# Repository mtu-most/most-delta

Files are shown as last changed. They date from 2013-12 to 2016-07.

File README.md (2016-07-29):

MOST-delta
==========
Development of the MOST Delta has halted as it has been superceded by <a href="https://github.com/phidiasllc/athena">Athena</a>.

A complete build process is available at http://www.appropedia.org/Delta_Build_Overview:MOST.

<h2>Highlights:</h2>
<ul>
<li>Magnetic tie rod ends</li>
<li>Actively cooled end effector</li>
<li>Attractive</li>
<li>Easy to build</li>
<li>Inexpensive, relatively short BOM</li>
<li>Thorough wiki-based build process with lots of illustrations</li>
<li>A rapidly growing user base</li>
<li>Very robust</li>
</ul>

<h2>Overview</h2>
The MOST delta printer is derived from the original Rostock (http://www.thingiverse.com/thing:17175). The design goal is to stay as true to RepRap ideals as possible, i.e. contain as many printed parts as possible. It's a very robust design and easier to build and calibrate than most delta printers.

<h2>Easter Egg in the SCAD</h2>
Dr. Who fans will want to keep an eye out!

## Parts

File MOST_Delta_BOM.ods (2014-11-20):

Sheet: BOM
Magnetic ball joint version
Part description | Print/Vitamin | Material | UOM | Count | Units | Total units | Functional Unit | Function
608zz bearing | Vitamin | bearing | ea | 6 |  | 6 | Idler end | idler bearing
608zz bearing | Vitamin | bearing | ea | 1 |  | 1 | Extruder drive
LM8UU bearing | Vitamin | bearing | ea | 6 |  | 6 | Apex | carriage linear bearing
MR105zz 5mm x 10mm x 4mm bearing | Vitamin | bearing | ea | 1 |  | 1 | Extruder drive
3/8” od ring magnets | Vitamin | magnet | ea | 12 |  | 12 | Tie rod | tie rod ends
T5 timing belt | Vitamin | belting | mm | 3 | 1350 | 4050 | Apex | timing belt
0.25” OD x 0.222” ID Al tubing | Vitamin | Al tube | mm | 6 | 242 | 1452 | Tie rod | Tie rod
3/8” G25 ball bearings | Vitamin | magnet | mm | 12 | 20 | 240 | Tie rod | tie rod pivot
18-Gauge 2 Conductor | Vitamin | conductor | m | 1 |  | 1 | End effector | hot end power
1m twisted pair | Vitamin | conductor | m | 3 | 1 | 3 | Idler end | limit switch twisted pair
1m twisted pair | Vitamin | conductor | m | 2 |  | 2 | End effector | fan power and hot end thermistor
8mm diameter drill rod | Vitamin | drill rod | mm | 6 | 595 | 3570 | Apex | guide rod
12V 5A power supply | Vitamin | electronics | ea | 1 |  | 1 | Electronics
40mm x 40mm 12v fan | Vitamin | electronics | ea | 1 |  | 1 | End effector | active cooling
Limit switch | Vitamin | electronics | ea | 3 |  | 3 | Electronics | Limit switch
Melzi controller board | Vitamin | electronics | ea | 1 |  | 1 | Electronics
#6 x 3/4” sheet metal screw | Vitamin | fastener | ea | 12 |  | 12 | Motor end | motor end base plate mount
#6 x 3/4” sheet metal screw | Vitamin | fastener | ea | 18 |  | 18 | Motor end | motor end linking board mount
#6 x 3/4” sheet metal screw | Vitamin | fastener | ea | 12 |  | 12 | Idler end | idler end base plate mount
#6 x 3/4” sheet metal screw | Vitamin | fastener | ea | 18 |  | 18 | Idler end | idler end linking board mount
M2 washer | Vitamin | fastener | ea | 6 |  | 6 | Idler end | limit switch mount
M2 x 12mm socket head cap screw | Vitamin | fastener | ea | 6 |  | 6 | Idler end | limit switch mount
M2 x 12mm socket head cap screw | Vitamin | fastener | ea | 1 |  | 1 | End effector | hot end retainer
M3 nut | Vitamin | fastener | ea | 6 |  | 6 | Motor end | motor end pulley
M3 nut | Vitamin | fastener | ea | 6 |  | 6 | Motor end | motor end vertical board mount
M3 nut | Vitamin | fastener | ea | 3 |  | 3 | Carriage | carriage belt terminator mount
M3 nut | Vitamin | fastener | ea | 12 |  | 12 | Idler end | idler end guide rod clamp
M3 nut | Vitamin | fastener | ea | 6 |  | 6 | Idler end | idler end vertical board mount
M3 nut | Vitamin | fastener | ea | 2 |  | 2 | Extruder drive | Preload
M3 nut | Vitamin | fastener | ea | 12 |  | 12 | Frame | Melzi mount
M3 nut | Vitamin | fastener | ea | 12 |  | 12 | Motor end | motor end guide rod clamp
M3 threaded rod | Vitamin | fastener | mm | 6 | 85 | 510 | Motor end | motor end guide rod clamp
M3 threaded rod | Vitamin | fastener | mm | 6 | 85 | 510 | Idler end | idler end guide rod clamp
M3 washer | Vitamin | fastener | ea | 12 |  | 12 | Motor end | motor end motor mount
M3 washer | Vitamin | fastener | ea | 12 |  | 12 | Motor end | motor end guide rod clamp
M3 washer | Vitamin | fastener | ea | 6 |  | 6 | Motor end | motor end vertical board mount
M3 washer | Vitamin | fastener | ea | 3 |  | 3 | Carriage | carriage belt terminator mount
M3 washer | Vitamin | fastener | ea | 12 |  | 12 | Idler end | idler end guide rod clamp
M3 washer | Vitamin | fastener | ea | 12 |  | 12 | Idler end | idler end vertical board mount
M3 washer | Vitamin | fastener | ea | 2 |  | 2 | Extruder drive | Preload
M3 washer | Vitamin | fastener | ea | 16 |  | 16 | Frame | Melzi mount
M3 x 12mm socket head cap screw | Vitamin | fastener | ea | 2 |  | 2 | End effector | fan mount
M3 x 12mm socket head cap screw | Vitamin | fastener | ea | 3 |  | 3 | Carriage | Carriage limit switch adjustment
M3 x 14mm socket head cap screw | Vitamin | fastener | ea | 12 |  | 12 | Motor end | motor end motor mount
M3 x 16mm socket head cap screw | Vitamin | fastener | ea | 3 |  | 3 | Carriage | carriage belt terminator mount
M3 x 25mm socket head cap screw | Vitamin | fastener | ea | 1 |  | 1 | Extruder drive | Motor mount
M3 x 25mm socket head cap screw | Vitamin | fastener | ea | 4 |  | 4 | Frame | Melzi mount
M3 x 30mm socket head cap screw | Vitamin | fastener | ea | 2 |  | 2 | Extruder drive | motor end
M3 x 45mm socket head cap screw | Vitamin | fastener | ea | 2 |  | 2 | Extruder drive | Preload
M3 x 50mm screw | Vitamin | fastener | ea | 6 |  | 6 | Motor end | motor end vertical board mount
M3 x 50mm screw | Vitamin | fastener | ea | 6 |  | 6 | Idler end | idler end vertical board mount
M3 x 6mm button head cap screw | Vitamin | fastener | ea | 1 |  | 1 | Extruder drive | Motor mount
M3 x 8mm set screw | Vitamin | fastener | ea | 6 |  | 6 | Motor end | motor end pulley
M4 nut | Vitamin | fastener | ea | 1 |  | 1 | End effector | Bowden sheath retainer
M4 nut | Vitamin | fastener | ea | 1 |  | 1 | Extruder drive | Infeed tube sheath retainer
M4 nut | Vitamin | fastener | ea | 1 |  | 1 | Extruder drive | Bowden sheath retainer
#6 x 1/2” sheet metal screw | Vitamin | fastener | ea | 2 |  | 2 | Extruder drive | Mounting screws
M8 nut | Vitamin | fastener | ea | 3 |  | 3 | Idler end | idler shaft retainer
M8 washer | Vitamin | fastener | ea | 9 |  | 9 | Idler end | idler shaft
M8 x 40mm hex head bolt | Vitamin | fastener | ea | 3 |  | 3 | Idler end | idler shaft
J-head hot end, 1.75mm x 0.5mm | Vitamin | hot end | ea | 1 |  | 1 | End effector
NEMA17 stepper motor | Vitamin | motor | ea | 1 |  | 1 | Extruder drive
NEMA17 stepper motor | Vitamin | motor | ea | 3 |  | 3 | Motor end | motor end motor mount
12 tooth T5 pulley w/ D shaft | Print | PLA | ea | 3 |  | 3 | Motor end | pulley
Extruder drive body | Print | PLA | ea | 1 |  | 1 | Extruder drive
Airtripper's idler holder | Print | PLA | ea | 1 |  | 1 | Extruder drive
Airtripper's idler shaft | Print | PLA | ea | 1 |  | 1 | Extruder drive
Airtripper's tie rod | Print | PLA | ea | 1 |  | 1 | Extruder drive
carriage | Print | PLA | ea | 3 |  | 3 | Apex | carriage
End effector | Print | PLA | ea | 1 |  | 1 | End effector
End Idler | Print | PLA | ea | 3 |  | 3 | Idler end | idler end
End Motor | Print | PLA | ea | 3 |  | 3 | Motor end | motor end
Fixed belt terminator | Print | PLA | ea | 3 |  | 3 | Apex | long belt terminator
Free belt terminator | Print | PLA | ea | 3 |  | 3 | Apex | short belt terminator
340mm diameter x 12mm plywood | Vitamin | plywood | ea | 2 |  | 2 | Frame | base plates
42mm x 240mm x 12 mm plywood | Vitamin | plywood | ea | 3 |  | 3 | Motor end | Motor end linking board
42mm x 240mm x 12 mm plywood | Vitamin | plywood | ea | 3 |  | 3 | Idler end | Motor end linking board
60mm x 605mm x 12mm plywood | Vitamin | plywood | ea | 3 |  | 3 | Apex | vertical board
1” x 1/4” rubber fuel line | Vitamin | tubing | inch | 1 | 1 | 1 | Extruder drive
4mm OD x 2mm ID PTFE tubing | Vitamin | tubing | mm | 1 | 700 | 700 | End effector | Bowden sheath
4mm OD x 2mm ID PTFE tubing | Vitamin | tubing | mm | 1 | 50 | 50 | Extruder drive | Infeed tube
Small wire ties | Vitamin | wire tie | ea | 10 |  | 10 | Frame
Mk7 drive gear | Vitamin | drive gear | ea | 1 |  | 1 | Extruder drive
USB A to mini B | Vitamin | electronics | ea | 1 |  | 1 | Electronics
Heat shrink tubing | Vitamin | electronics | ea | 10
10” diameter mirror/glass | Vitamin | glass | ea | 1 |  | 1 | Frame | Build platform

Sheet: Pivot Table_BOM_1
Filter
Print/Vitamin | Vitamin
Part description | Material | Data
#6 x 1/2” sheet metal screw | fastener | Sum - Units
 |  | Sum - Count | 2
#6 x 3/4” sheet metal screw | fastener | Sum - Units
 |  | Sum - Count | 60
0.25” OD x 0.222” ID Al tubing | Al tube | Sum - Units | 242
 |  | Sum - Count | 6
1” x 1/4” rubber fuel line | tubing | Sum - Units | 1
 |  | Sum - Count | 1
10” diameter mirror/glass | glass | Sum - Units
 |  | Sum - Count | 1
12V 5A power supply | electronics | Sum - Units
 |  | Sum - Count | 1
18-Gauge 2 Conductor | conductor | Sum - Units
 |  | Sum - Count | 1
1m twisted pair | conductor | Sum - Units | 1
 |  | Sum - Count | 5
3/8” G25 ball bearings | magnet | Sum - Units | 20
 |  | Sum - Count | 12
3/8” od ring magnets | magnet | Sum - Units
 |  | Sum - Count | 12
340mm diameter x 12mm plywood | plywood | Sum - Units
 |  | Sum - Count | 2
40mm x 40mm 12v fan | electronics | Sum - Units
 |  | Sum - Count | 1
42mm x 240mm x 12 mm plywood | plywood | Sum - Units
 |  | Sum - Count | 6
4mm OD x 2mm ID PTFE tubing | tubing | Sum - Units | 750
 |  | Sum - Count | 2
608zz bearing | bearing | Sum - Units
 |  | Sum - Count | 7
60mm x 605mm x 12mm plywood | plywood | Sum - Units
 |  | Sum - Count | 3
8mm diameter drill rod | drill rod | Sum - Units | 595
 |  | Sum - Count | 6
Heat shrink tubing | electronics | Sum - Units
 |  | Sum - Count | 10
J-head hot end, 1.75mm x 0.5mm | hot end | Sum - Units
 |  | Sum - Count | 1
Limit switch | electronics | Sum - Units
 |  | Sum - Count | 3
LM8UU bearing | bearing | Sum - Units
 |  | Sum - Count | 6
M2 washer | fastener | Sum - Units
 |  | Sum - Count | 6
M2 x 12mm socket head cap screw | fastener | Sum - Units
 |  | Sum - Count | 7
M3 nut | fastener | Sum - Units
 |  | Sum - Count | 59
M3 threaded rod | fastener | Sum - Units | 170
 |  | Sum - Count | 12
M3 washer | fastener | Sum - Units
 |  | Sum - Count | 75
M3 x 12mm socket head cap screw | fastener | Sum - Units
 |  | Sum - Count | 5
M3 x 14mm socket head cap screw | fastener | Sum - Units
 |  | Sum - Count | 12
M3 x 16mm socket head cap screw | fastener | Sum - Units
 |  | Sum - Count | 3
M3 x 25mm socket head cap screw | fastener | Sum - Units
 |  | Sum - Count | 5
M3 x 30mm socket head cap screw | fastener | Sum - Units
 |  | Sum - Count | 2
M3 x 45mm socket head cap screw | fastener | Sum - Units
 |  | Sum - Count | 2
M3 x 50mm screw | fastener | Sum - Units
 |  | Sum - Count | 12
M3 x 6mm button head cap screw | fastener | Sum - Units
 |  | Sum - Count | 1
M3 x 8mm set screw | fastener | Sum - Units
 |  | Sum - Count | 6
M4 nut | fastener | Sum - Units
 |  | Sum - Count | 3
M8 nut | fastener | Sum - Units
 |  | Sum - Count | 3
M8 washer | fastener | Sum - Units
 |  | Sum - Count | 9
M8 x 40mm hex head bolt | fastener | Sum - Units
 |  | Sum - Count | 3
Melzi controller board | electronics | Sum - Units
 |  | Sum - Count | 1
Mk7 drive gear | drive gear | Sum - Units
 |  | Sum - Count | 1
MR105zz 5mm x 10mm x 4mm bearing | bearing | Sum - Units
 |  | Sum - Count | 1
NEMA17 stepper motor | motor | Sum - Units
 |  | Sum - Count | 4
Small wire ties | wire tie | Sum - Units
 |  | Sum - Count | 10
T5 timing belt | belting | Sum - Units | 1350
 |  | Sum - Count | 3
USB A to mini B | electronics | Sum - Units
 |  | Sum - Count | 1
Total Sum - Units |  |  | 3129
Total Sum - Count |  |  | 394

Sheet: Sources
Part description | Part number | Unit description | Sold in units of | URL
M2 washer | 7364 | pack | 100 | http://www.boltdepot.com/Product-Details.aspx?product=7364
M2 x 10mm socket head cap screw | 6366 | pack | 100 | http://www.boltdepot.com/Product-Details.aspx?product=6366
M3 nut | 4773 | pack | 1000 | http://www.boltdepot.com/Product-Details.aspx?product=4773
M3 threaded rod | 90024A040 | mm | 1000 | mcmaster.com
M3 washer | 4513 | pack | 1000 | http://www.boltdepot.com/Product-Details.aspx?product=4513
M3 x 12mm socket head cap screw | 6381 | pack | 100 | http://www.boltdepot.com/Product-Details.aspx?product=6381
M3 x 14mm socket head cap screw | 91292A027 | pack | 100 | mcmaster.com
M3 x 16mm socket head cap screw | 6382 | pack | 100 | http://www.boltdepot.com/Product-Details.aspx?product=6382
M3 x 25mm socket head cap screw | 6384 | pack | 100 | http://www.boltdepot.com/Product-Details.aspx?product=6384
M3 x 30mm socket head cap screw | 6385 | pack | 100 | http://www.boltdepot.com/Product-Details.aspx?product=6385
M3 x 45mm socket head cap screw | 6388 | pack | 100 | http://www.boltdepot.com/Product-Details.aspx?product=6388
M3 x 50mm screw | 6389 | pack | 1000 | http://www.boltdepot.com/Product-Details.aspx?product=6389
M3 x 6mm button head cap screw | 92095A179 | pack | 100 | mcmaster.com
M3 x 8mm set screw | 92015A105 | pack | 50 | mcmaster.com
#6 x 3/4” sheet metal screw | 14712 | pack | 1000 | http://www.boltdepot.com/Product-Details.aspx?product=14712
M4 nut | 4774 | pack | 100 | http://www.boltdepot.com/Product-Details.aspx?product=4774
#6 x 1/2” sheet metal screw | 14710 | pack | 100 | http://www.boltdepot.com/Product-Details.aspx?product=14710
M4 x 12mm socket head cap screw | 91292A117 | pack | 100 | mcmaster.com
M4 x 20mm socket head cap screw | 91292A121 | pack | 100 | mcmaster.com
M8 nut | 91828A410 | pack | 50 | mcmaster.com
M8 washer | 93475A270 | pack | 100 | mcmaster.com
M8 x 40mm hex head bolt | 91287A305 | pack | 100 | http://www.boltdepot.com/Product-Details.aspx?product=5817
8mm diameter drill rod | 8116K37 | mm | 1828.8 | mcmaster.com
4mm OD x 2mm ID PTFE tubing | 2129T24 | mm | 304.8 | mcmaster.com
0.25” OD x 0.222” ID Al tubing |  | mm | 1 | http://www3.towerhobbies.com/cgi-bin/wti0001p?&I=LXDTWL&P=7
3/8” od ring magnets | R622CS-P | ea | 2 | https://www.kjmagnetics.com/proddetail.asp?prod=R622CS-P
3/8” G25 ball bearings |  | pack | 1 | http://www.amazon.com/gp/product/B002BBD4SG/ref=oh_details_o08_s00_i00?ie=UTF8&psc=1
608zz bearing |  | pack | 1 | http://rp3d.com
LM8UU bearing |  | pack | 1 | http://rp3d.com
MR105zz 5mm x 10mm x 4mm bearing |  | pack | 1 | http://rp3d.com
T5 timing belt |  | mm | 304.8 | http://shop.polybelt.com/6T5-Open-End-Belt-Roll-Polyurethane-with-Steel-Cords-B6T5-MPS.htm
16-Gauge 2 Conductor |  | mm | 30480 | http://www.amazon.com/Mediabridge-Gauge-Speaker-Wire-Feet/dp/B0044YPN0A
Limit switch | SW767-ND | ea | 1 | http://www.digikey.com/product-detail/en/SS-3GLPT/SW767-ND/664728
12V 5A power supply |  | ea | 1 | Amazon.com
40mm x 40mm 12v fan |  | ea | 1 | http://www.kysanelectronics.com/Products/Detail.php?recordID=7738
Melzi controller board |  | ea | 1 | http://www.rp3d.com/10pcs-melzi-of-3d-printer-p-20.html
NEMA17 stepper motor |  | ea | 1 | http://www.kysanelectronics.com/Products/Detail.php?recordID=7850
J-head hot end, 1.75mm x 0.5mm |  | ea | 1 | hotends.com
1” x 1/4” rubber fuel line |  | mm | 304.8 | http://www.amazon.com/Dayco-80057-Fuel-Line-Roll/dp/B000CIZV7C
Mk7 drive gear |  | ea | 1 | http://twelvepro.com/index.php?route=product/product&product_id=51
USB A to mini B |  | ea | 1 | http://rp3d.com
10” mirror circle |  | ea | 1 | http://www.consumercrafts.com/store/details/catalog/floral-round-mirrors/1635-70

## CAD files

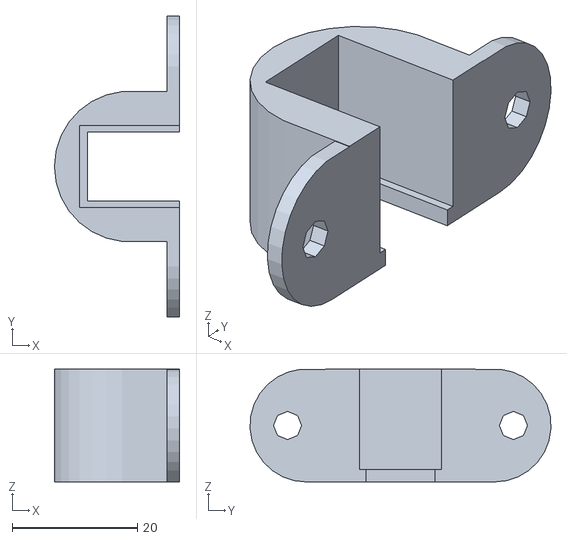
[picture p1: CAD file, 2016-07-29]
STL/barrel_connector.stl
19.9 x 48.0 x 18.0

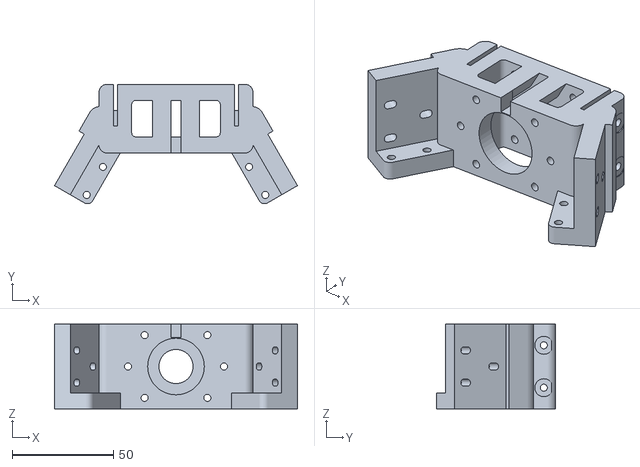
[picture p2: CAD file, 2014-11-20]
STL/end_motor.stl
120.2 x 59.1 x 42.0

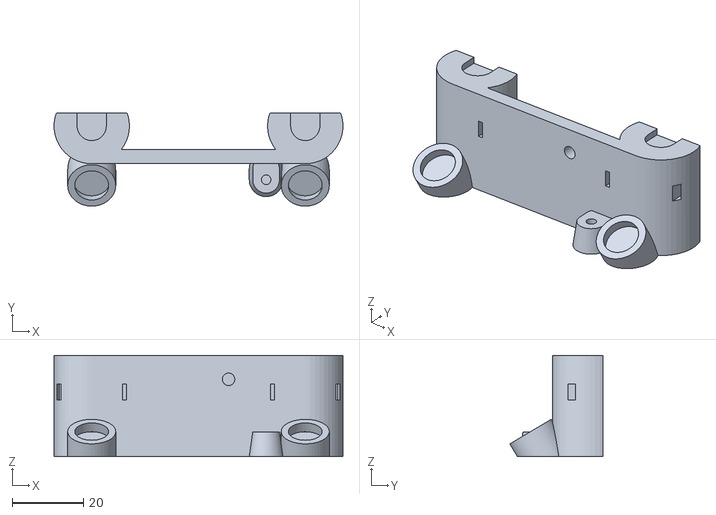
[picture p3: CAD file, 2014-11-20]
STL/carriage.stl
81.2 x 26.2 x 28.5

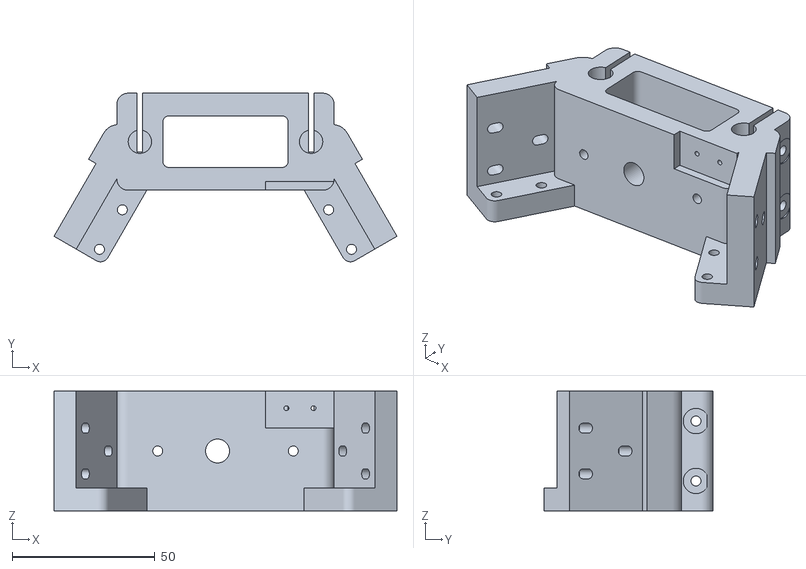
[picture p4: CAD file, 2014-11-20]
STL/end_idler.stl
120.2 x 59.1 x 42.0

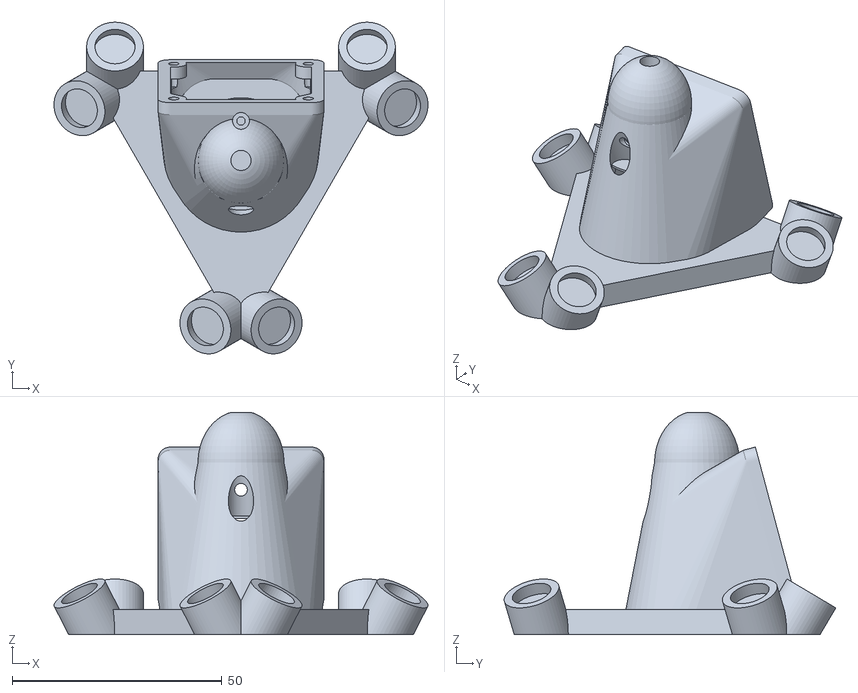
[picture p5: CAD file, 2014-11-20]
STL/effector.stl
89.1 x 79.0 x 52.9

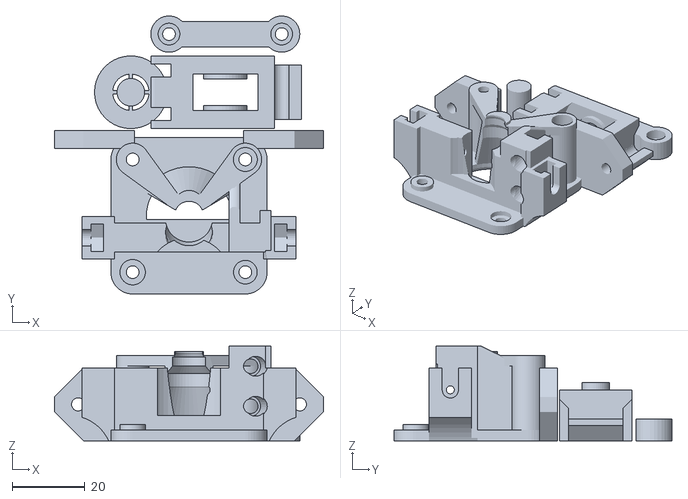
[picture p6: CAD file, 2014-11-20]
STL/extdrive.stl
74.0 x 76.5 x 26.0

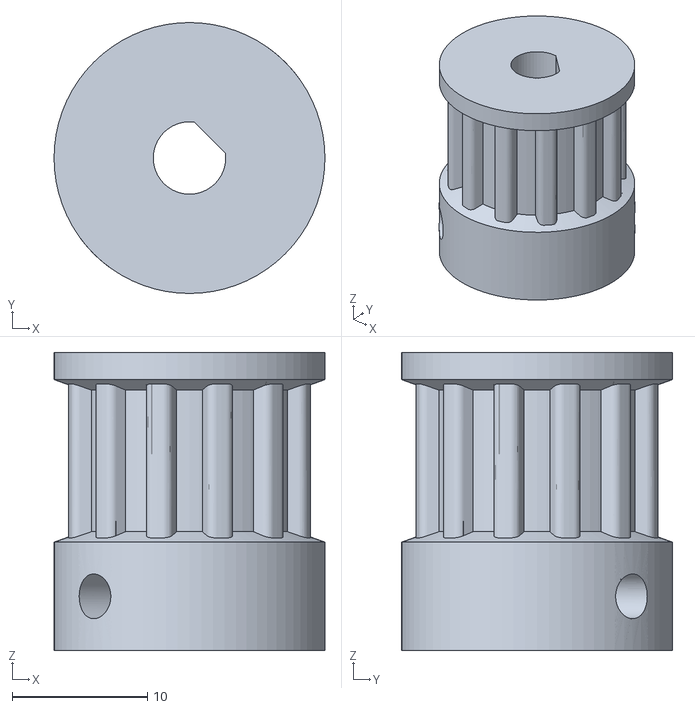
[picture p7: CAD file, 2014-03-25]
STL/12toothT5_Dshaft.stl
20.0 x 20.0 x 22.0

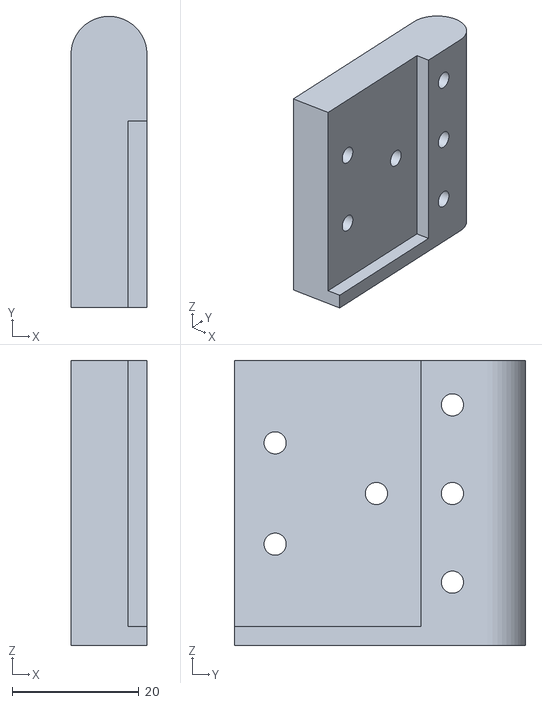
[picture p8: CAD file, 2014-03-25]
STL/linking_brd_template.stl
12.0 x 46.0 x 45.0

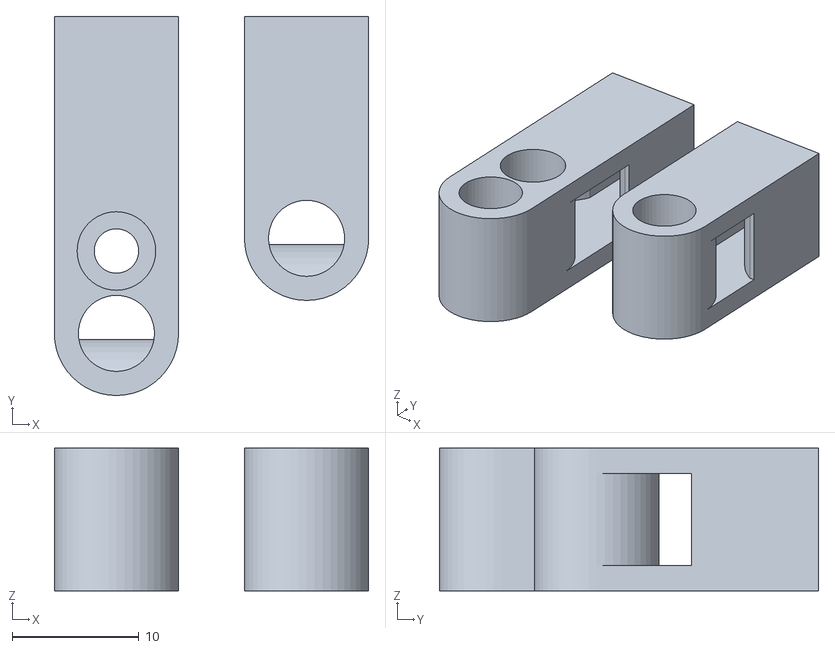
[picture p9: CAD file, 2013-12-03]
STL/belt_terminators.stl
24.8 x 29.9 x 11.2

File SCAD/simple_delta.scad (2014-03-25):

include <fasteners.scad>
include <bearings.scad>
include <NEMA17.scad>
include <cog.scad>
include <Triangles.scad>
include <hotends.scad>
include <belt_terminator.scad>

// [w, l, t] = [y, x, z]
$fn = 48;

//render_part(9);

//plates(3);

magnet_mounts = true;


module plates(plate) {
	if (plate == 1) {
		for (i = [0:2])
			rotate([0, 0, i * 120]) {
				translate([-15, r_effector + 18, t_carriage / 2])
					carriage(dogged = false, magnet_mounts = magnet_mounts, stage_mounts = false);
			
				translate([-20, r_effector + 18, 0])
					rotate([0, 0, 90])
						terminator(l_pass = 10, flag = false, mount = true, magnet = false);
			
				translate([37, r_effector + 10, 0])
					rotate([0, 0, 90])
							terminator(l_pass = 10, flag = 0, mount = 0);
			}

		translate([0, 0, t_effector / 2])
			effector(dalekify = false, magnet_mounts = magnet_mounts);
	}
	
	if (plate == 2) {
		end_motor();
		
		translate([65, 5, 0])
			rotate([0, 0, -60])
				end_motor();
		
		translate([30, -58, 0])
			rotate([0, 0, -60])
				end_motor();
	}

	if (plate == 3) {
		end_idler();
		
		translate([65, 5, 0])
			rotate([0, 0, -60])
				end_idler();
		
		translate([30, -58, 0])
			rotate([0, 0, -60])
				end_idler();
	}
}

module render_part(part_to_render) {
	if (part_to_render == 1) end_motor();

	if (part_to_render == 2) end_idler();

	if (part_to_render == 3) carriage(dogged = false, magnet_mounts = magnet_mounts, stage_mounts = false);

	if (part_to_render == 4) effector(dalekify = false, magnet_mounts = magnet_mounts);

	if (part_to_render == 5) hook();

	if (part_to_render == 6) power_entry();

	if (part_to_render == 7) intermediate();

	if (part_to_render == 8) stage_effector(magnet_mounts = 1);

	if (part_to_render == 9) linking_board_template();

	if (part_to_render == 10) assembly();

	if (part_to_render == 11) camera_carriage();
	
	if (part_to_render == 12) limit_switch_mount();

	if (part_to_render == 13) stage_pcb_dovetail();

	if (part_to_render == 14) stage_pcb_dovetail_clamp();
}

// printer dims
r_printer = 203.5; // radius of the printer - typically 175; 203.5 yields exact same geometry with 12" Al rod and 3/8" bearing
l_tie_rod = 312.477; // length of the tie rods - typically 250; with 12" Al rod + 3/8" bearing = 312.477
l_guide_rods = 300; // length of the guide rods - only used for assembly

// belt, pulley and idler dims
od_idler = od_608; // idler OD
id_idler = id_608; // idler id
h_idler = h_608; // thickness of idler
h_idler_washer = h_M8_washer; // idler bearing washer
w_belt = 6; // width of the belt (not used)
d_pulley = 16.9; // diameter of the pulley (used to center idler)

// guide rod and clamp dims
cc_guides = 60; // center-to-center of the guide rods
d_guides = 8.2;//8.5; // diameter of the guide rods
pad_clamp = 8; // additional material around guide rods
gap_clamp = 2; // opening for clamp

// following for tabs on either side of clamp to which linking boards are attached
// the radius of the delta measured from the center of the guide rods to the center of the triangle
// as drawn here, the tangent is parallel to the x-axis and the guide rod centers lie on y=0
cc_mount = 75; // tangential distance from center of guide rods to side mount pivot point
w_mount = 12; // thickness of the tabs the boards making up the triangle sides will attach to
l_mount = 40; // length of said tabs
cc_mount_holes = 16;
l_base_mount = l_mount;
w_base_mount = 14.1;
t_base_mount = 8.0;
r_base_mount = 3;
l_mount_slot = 2; // length of the slot for mounting screw holes

// various radii and chord lengths
a_arc_guides = asin(cc_guides / 2 / r_printer); // angle of arc between guide rods at r_printer 
a_sep_guides = 120 - 2 * a_arc_guides; // angle of arc between nearest rods on neighboring apexes
l_chord_guides = 2 * r_printer * sin(a_sep_guides / 2); // length of chord between nearest rods on neighboring apexes
r_tower_center = pow(pow(r_printer, 2) - pow(cc_guides / 2, 2), 0.5); // radius to centerline of apex
r_mount_pivot = pow(pow(r_tower_center, 2) + pow(cc_mount / 2, 2), 0.5); // radius to pivot point of apex mounts
a_arc_mount = asin(cc_mount / 2 / r_mount_pivot);// angle subtended by arc struck between apex centerline and mount pivot point
a_sep_mounts = 120 - 2 * a_arc_mount; // angle subtended by arc struck between mount pivot points between adjacent apexes
l_chord_pivots = 2 * r_mount_pivot * sin(a_sep_mounts / 2); // chord length between adjacent mount pivot points

// remove enough material from mount so that a logical length board can be cut to ensure adjacent mount pivot point chord lengths will yield a printer having r_printer
l_brd = floor(l_chord_pivots / 10) * 10 - l_mount / 2; // length of the board that will be mounted between the apexs to yield r_printer
l_pad_mount = (l_chord_pivots - l_brd) / 2;
l_boss_mount = l_mount - l_pad_mount;

l_idler_relief = cc_guides - d_guides - pad_clamp;
w_idler_relief = 2 * (h_idler + h_idler_washer) + 1;
r_idler_relief = 2; // radius of the relief inside the apex
l_clamp = cc_guides + d_guides + pad_clamp;
w_clamp = w_idler_relief + pad_clamp + 8;
t_clamp = l_NEMA17;//od_idler + 6;

// ball joint mount dimensions
l_ball_joint = 7 + h_M3_washer;
d_ball_joint = 6;
d_ball_socket = 10; // diameter of the ball joint socket
d_mount_ball_joint = d_ball_joint + 4;
l_mount_ball_joint = l_ball_joint + 6;
offset_mount = 3;

// effector dims
l_effector = 60; // this needs to be played with to keep the fan from hitting the tie rods
H_effector = equilateral_height_from_base(l_effector);
r_effector = l_effector * tan(30) / 2 + (magnet_mounts == 1) ? d_mount_ball_joint : 29;
t_effector = 6;
h_triangle_inner = H_effector + 12;
r_triangle_middle = equilateral_base_from_height(h_triangle_inner) * tan(30) / 2;
d_175_sheath = 4.8;
175_bowden = [d_M4_nut, h_M4_nut, d_175_sheath];

// carriage dims:
w_carriage_web = 4;
t_carriage = l_lm8uu + 4;
carriage_offset = 18; // distance from center of guide rods to center of ball mount pivot
y_offset_endstop = -od_lm8uu / 2 - 8;
l_limit_switch = 24;
w_limit_switch = 6;
t_limit_switch = 14;

// magnetic ball joint dims
d_ball_bearing = 3 * 25.4 / 8;
id_magnet = 15 * 25.4 / 64;
od_magnet = 3 * 25.4 / 8;
h_magnet = 25.4 / 8;
r_bearing_seated = pow(pow(d_ball_bearing / 2, 2) - pow(id_magnet / 2, 2), 0.5); // depth ball bearing sinks into magnet id
h_carriage_magnet_mount = 9;
h_effector_magnet_mount = 10;
r_pad_carriage_magnet_mount = 2;
r_pad_effector_magnet_mount = 1.5;

// center-to-center of tie rod pivots
tie_rod_angle = acos((r_printer - r_effector - carriage_offset) / l_tie_rod);

echo(str("Printer radius = ", r_printer));
echo(str("Effector offset = ", r_effector, "mm"));
echo(str("Carriage offset = ", carriage_offset, "mm"));
echo(str("Printer effective radius = ", r_printer - r_effector - carriage_offset));
echo(str("Distance between nearest neighbor guide rods = ", l_chord_guides, "mm"));
echo(str("Radius to centerline of tower = ", r_tower_center, "mm"));
echo(str("Radius to mount tab pivot = ", r_mount_pivot, "mm"));
echo(str("Distance between adjacent mount pivot points = ", l_chord_pivots, "mm"));
echo(str("Length of linking board to yield printer radius of ", r_printer, "mm  = ", l_brd, "mm"));
echo(str("Linking board tab thickness = ", t_clamp, "mm"));
echo(str("Linking board hole c-c = ", cc_mount_holes, "mm"));
echo(str("Linking board hole offset from end = ", floor(l_pad_mount / 2), "mm"));
echo(str("Linking board-tab overlap = ", l_boss_mount, "mm"));
echo(str("Radius of base plate = ", ceil(r_printer - d_guides / 2 - 1), "mm"));
echo(str("Tie rod angle at (0, 0, 0) = ", tie_rod_angle));
echo(str("Effector tie rod c-c = ", l_effector, " mm"));

module limit_switch_mount() {
	difference() {
		union() {
			cylinder(r = d_guides / 2 + 4, h = 14, center = true);
			
			translate([d_guides / 2 + 2, 15, 7])
				cube([4, 30, 28], center = true);
				
			translate([-3.75, d_guides - 2, 0])
				rotate([0, 90, 0])
					hull() {
						cube([14, 4, 4], center = true);
						
						translate([0, d_M3_screw + 2, 0])
							cylinder(r = d_M3_screw / 2 + 3, h = 4, center = true);
				}
		}

		cylinder(r = d_guides / 2, h = 15, center = true);
		
		translate([d_guides / 2 - 3, 10, 0])
			cube([6, 20, 15], center = true);
		
		translate([0, d_guides + 3.75, 0])
			rotate([0, 90, 0])
				cylinder(r = d_M3_screw / 2, h = 20, center = true);
				
		translate([d_guides / 2 + 2, 13 + d_guides / 2, 16])
			rotate([0, 90, 0])
				for (i = [-1, 1])
					translate([0, i * 5, 0])
						cylinder(r = 0.8, h = 6, center = true);
	}
}

module mount_body(
	l_base_mount,
	w_base_mount,
	t_base_mount,
	r_base_mount,
	l_linking_board_slot = 0,
	hole_count = 3) {

	difference() {
		hull() {
			cylinder(r = w_mount / 2, h = t_clamp, center = true);

			translate([0, -l_mount + w_mount / 2, 0])
				cube([w_mount, w_mount, t_clamp], center = true);
		}
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

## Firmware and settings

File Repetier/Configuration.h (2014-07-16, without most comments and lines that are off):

#define CONFIGURATION_H
#define NUM_EXTRUDER 1
#define MOTHERBOARD 63
#include "pins.h"
#define DRIVE_SYSTEM 3
#if DRIVE_SYSTEM==3
#define DELTA_DRIVE_TYPE 0
#if DELTA_DRIVE_TYPE == 0
#define BELT_PITCH 5
#define PULLEY_TEETH 12
#define PULLEY_CIRCUMFERENCE (BELT_PITCH * PULLEY_TEETH)
#elif DELTA_DRIVE_TYPE == 1
#define PULLEY_DIAMETER 10
#define PULLEY_CIRCUMFERENCE (PULLEY_DIAMETER * 3.1415927)
#endif
#define STEPS_PER_ROTATION 200
#define MICRO_STEPS 16
#define AXIS_STEPS_PER_MM ((float)(MICRO_STEPS * STEPS_PER_ROTATION) / PULLEY_CIRCUMFERENCE)
#define XAXIS_STEPS_PER_MM AXIS_STEPS_PER_MM
#define YAXIS_STEPS_PER_MM AXIS_STEPS_PER_MM
#define ZAXIS_STEPS_PER_MM AXIS_STEPS_PER_MM
#else
#define XAXIS_STEPS_PER_MM 98.425196
#define YAXIS_STEPS_PER_MM 98.425196
#define ZAXIS_STEPS_PER_MM 2560
#endif
#define EXTRUDER_FAN_COOL_TEMP 50
#define EXT0_X_OFFSET 0
#define EXT0_Y_OFFSET 0
#define EXT0_STEPS_PER_MM 92
#define EXT0_TEMPSENSOR_TYPE 97
#define EXT0_TEMPSENSOR_PIN TEMP_0_PIN
#define EXT0_HEATER_PIN HEATER_0_PIN
#define EXT0_STEP_PIN E0_STEP_PIN
#define EXT0_DIR_PIN E0_DIR_PIN
#define EXT0_INVERSE true
#define EXT0_ENABLE_PIN E0_ENABLE_PIN
#define EXT0_ENABLE_ON false
#define EXT0_MAX_FEEDRATE 30
#define EXT0_MAX_START_FEEDRATE 10
#define EXT0_MAX_ACCELERATION 4000
#define EXT0_HEAT_MANAGER 0
#define EXT0_WATCHPERIOD 1
#define EXT0_PID_INTEGRAL_DRIVE_MAX 140
#define EXT0_PID_INTEGRAL_DRIVE_MIN 60
#define EXT0_PID_P   24
#define EXT0_PID_I   0.88
#define EXT0_PID_D 80
#define EXT0_PID_MAX 255
#define EXT0_ADVANCE_K 0.0f
#define EXT0_ADVANCE_L 0.0f
#define EXT0_ADVANCE_BACKLASH_STEPS 0
#define EXT0_WAIT_RETRACT_TEMP 		150
#define EXT0_WAIT_RETRACT_UNITS 	0
#define EXT0_SELECT_COMMANDS "M117 Extruder 1"
#define EXT0_DESELECT_COMMANDS ""
#define EXT0_EXTRUDER_COOLER_PIN -1
#define EXT0_EXTRUDER_COOLER_SPEED 255
#define RETRACT_DURING_HEATUP false
#define PID_CONTROL_RANGE 20
#define EXTRUDE_MAXLENGTH 100
#define SKIP_M109_IF_WITHIN 2
#define SCALE_PID_TO_MAX 0
#define HEATER_PWM_SPEED 1 // How fast ist pwm signal 0 = 15.25Hz, 1 = 30.51Hz, 2 = 61.03Hz, 3 = 122.06Hz
#define NUM_TEMPS_USERTHERMISTOR0 28
#define USER_THERMISTORTABLE0  {\
  {1*4,864*8},{21*4,300*8},{25*4,290*8},{29*4,280*8},{33*4,270*8},{39*4,260*8},{46*4,250*8},{54*4,240*8},{64*4,230*8},{75*4,220*8},\
  {90*4,210*8},{107*4,200*8},{128*4,190*8},{154*4,180*8},{184*4,170*8},{221*4,160*8},{265*4,150*8},{316*4,140*8},{375*4,130*8},\
  {441*4,120*8},{513*4,110*8},{588*4,100*8},{734*4,80*8},{856*4,60*8},{938*4,40*8},{986*4,20*8},{1008*4,0*8},{1018*4,-20*8}	}
#define NUM_TEMPS_USERTHERMISTOR1 0
#define USER_THERMISTORTABLE1  {}
#define NUM_TEMPS_USERTHERMISTOR2 0
#define USER_THERMISTORTABLE2  {}
#define USE_GENERIC_THERMISTORTABLE_1
#define GENERIC_THERM1_T0 25
#define GENERIC_THERM1_R0 100000
#define GENERIC_THERM1_BETA 3887
#define GENERIC_THERM1_MIN_TEMP -60
#define GENERIC_THERM1_MAX_TEMP 300
#define GENERIC_THERM1_R1 0
#define GENERIC_THERM1_R2 10000
#define GENERIC_THERM2_T0 170
#define GENERIC_THERM2_R0 1042.7
#define GENERIC_THERM2_BETA 4036
#define GENERIC_THERM2_MIN_TEMP -20
#define GENERIC_THERM2_MAX_TEMP 300
#define GENERIC_THERM2_R1 0
#define GENERIC_THERM2_R2 4700
#define GENERIC_THERM3_T0 170
#define GENERIC_THERM3_R0 1042.7
#define GENERIC_THERM3_BETA 4036
#define GENERIC_THERM3_MIN_TEMP -20
#define GENERIC_THERM3_MAX_TEMP 300
#define GENERIC_THERM3_R1 0
#define GENERIC_THERM3_R2 4700
#define GENERIC_THERM_VREF 5
#define GENERIC_THERM_NUM_ENTRIES 33
#define HAVE_HEATED_BED false
#define HEATED_BED_MAX_TEMP 115
#define SKIP_M190_IF_WITHIN 3
#define HEATED_BED_SENSOR_TYPE 1
#define HEATED_BED_SENSOR_PIN TEMP_1_PIN
#define HEATED_BED_HEATER_PIN HEATER_1_PIN
#define HEATED_BED_SET_INTERVAL 5000
#define HEATED_BED_HEAT_MANAGER 1
#define HEATED_BED_PID_INTEGRAL_DRIVE_MAX 255
#define HEATED_BED_PID_INTEGRAL_DRIVE_MIN 80
#define HEATED_BED_PID_PGAIN   196
#define HEATED_BED_PID_IGAIN   33.02
#define HEATED_BED_PID_DGAIN 290
#define HEATED_BED_PID_MAX 255
#define MAXTEMP 260
#define MIN_DEFECT_TEMPERATURE -10
#define MAX_DEFECT_TEMPERATURE 300
#define ENDSTOP_PULLUP_X_MIN false
#define ENDSTOP_PULLUP_Y_MIN false
#define ENDSTOP_PULLUP_Z_MIN false
#define ENDSTOP_PULLUP_X_MAX true
#define ENDSTOP_PULLUP_Y_MAX true
#define ENDSTOP_PULLUP_Z_MAX true
#define ENDSTOP_X_MIN_INVERTING false
#define ENDSTOP_Y_MIN_INVERTING false
#define ENDSTOP_Z_MIN_INVERTING false
#define ENDSTOP_X_MAX_INVERTING false
#define ENDSTOP_Y_MAX_INVERTING false
#define ENDSTOP_Z_MAX_INVERTING false
#define MIN_HARDWARE_ENDSTOP_X false
#define MIN_HARDWARE_ENDSTOP_Y false
#define MIN_HARDWARE_ENDSTOP_Z false
#define MAX_HARDWARE_ENDSTOP_X true
#define MAX_HARDWARE_ENDSTOP_Y true
#define MAX_HARDWARE_ENDSTOP_Z true
#define X_ENABLE_ON 0
#define Y_ENABLE_ON 0
#define Z_ENABLE_ON 0
#define DISABLE_X false
#define DISABLE_Y false
#define DISABLE_Z false
#define DISABLE_E false
#define INVERT_X_DIR true
#define INVERT_Y_DIR true
#define INVERT_Z_DIR true
#define X_HOME_DIR 1
#define Y_HOME_DIR 1
#define Z_HOME_DIR 1
#define max_software_endstop_r true
#define min_software_endstop_x false
#define min_software_endstop_y false
#define min_software_endstop_z false
#define max_software_endstop_x false
#define max_software_endstop_y false
#define max_software_endstop_z false
#define ENDSTOP_X_BACK_MOVE 5
#define ENDSTOP_Y_BACK_MOVE 5
#define ENDSTOP_Z_BACK_MOVE 2
#define ENDSTOP_X_RETEST_REDUCTION_FACTOR 8
#define ENDSTOP_Y_RETEST_REDUCTION_FACTOR 8
#define ENDSTOP_Z_RETEST_REDUCTION_FACTOR 8
#define ENDSTOP_X_BACK_ON_HOME 0
#define ENDSTOP_Y_BACK_ON_HOME 0
#define ENDSTOP_Z_BACK_ON_HOME 0
#define ALWAYS_CHECK_ENDSTOPS true
#define X_MAX_LENGTH 200
#define Y_MAX_LENGTH 200
#define Z_MAX_LENGTH 247
#define X_MIN_POS 0
#define Y_MIN_POS 0
#define Z_MIN_POS 0
#define MICROSTEP_MODES {8,8,8,8,8} // [1,2,4,8,16]
#if MOTHERBOARD==301
#define MOTOR_CURRENT {135,135,135,135,135} // Values 0-255 (RAMBO 135 = ~0.75A, 185 = ~1A)
#elif MOTHERBOARD==12
#define MOTOR_CURRENT {35713,35713,35713,35713,35713} // Values 0-65535 (3D Master 35713 = ~1A)
#endif
#define DELTA_SEGMENTS_PER_SECOND_PRINT 180 // Move accurate setting for print moves
#define DELTA_SEGMENTS_PER_SECOND_MOVE 70 // Less accurate setting for other moves
#if DRIVE_SYSTEM==3
#define DELTA_DIAGONAL_ROD 250.5 // mm
#define DELTA_ALPHA_A 210
#define DELTA_ALPHA_B 330
#define DELTA_ALPHA_C 90
#define DELTA_RADIUS_CORRECTION_A 0
#define DELTA_RADIUS_CORRECTION_B 0
#define DELTA_RADIUS_CORRECTION_C 0
#define DELTA_DIAGONAL_CORRECTION_A 0
#define DELTA_DIAGONAL_CORRECTION_B 0
#define DELTA_DIAGONAL_CORRECTION_C 0
#define DELTA_MAX_RADIUS 200
#define END_EFFECTOR_HORIZONTAL_OFFSET 0
#define CARRIAGE_HORIZONTAL_OFFSET 0
#define PRINTER_RADIUS 126
#define DELTA_RADIUS (PRINTER_RADIUS-END_EFFECTOR_HORIZONTAL_OFFSET-CARRIAGE_HORIZONTAL_OFFSET)
#define DELTA_HOME_ON_POWER false
#define DELTA_X_ENDSTOP_OFFSET_STEPS 0
#define DELTA_Y_ENDSTOP_OFFSET_STEPS 0
#define DELTA_Z_ENDSTOP_OFFSET_STEPS 0
#define SOFTWARE_LEVELING
#endif
#define MAX_DELTA_SEGMENTS_PER_LINE 22
#define STEPPER_INACTIVE_TIME 360
#define MAX_INACTIVE_TIME 0L
#define MAX_FEEDRATE_X 2000
#define MAX_FEEDRATE_Y 2000
#define MAX_FEEDRATE_Z 2000
#define HOMING_FEEDRATE_X 100
#define HOMING_FEEDRATE_Y 100
#define HOMING_FEEDRATE_Z 100
#define HOMING_ORDER HOME_ORDER_ZXY
#define ENABLE_BACKLASH_COMPENSATION false
#define Z_BACKLASH 0
#define X_BACKLASH 0
#define Y_BACKLASH 0
#define RAMP_ACCELERATION 1
#define STEPPER_HIGH_DELAY 0
#define STEP_DOUBLER_FREQUENCY 12000
#define ALLOW_QUADSTEPPING true
#define DOUBLE_STEP_DELAY 1 // time in microseconds
#define MAX_HALFSTEP_INTERVAL 1999
#define MAX_ACCELERATION_UNITS_PER_SQ_SECOND_X 3000
#define MAX_ACCELERATION_UNITS_PER_SQ_SECOND_Y 3000
#define MAX_ACCELERATION_UNITS_PER_SQ_SECOND_Z 3000
#define MAX_TRAVEL_ACCELERATION_UNITS_PER_SQ_SECOND_X 5000
#define MAX_TRAVEL_ACCELERATION_UNITS_PER_SQ_SECOND_Y 5000
#define MAX_TRAVEL_ACCELERATION_UNITS_PER_SQ_SECOND_Z 5000
#define MAX_JERK 20.0
#define MAX_ZJERK 0.3
#define MOVE_CACHE_SIZE 16
#define MOVE_CACHE_LOW 10
#define LOW_TICKS_PER_MOVE 250000
#define MIN_EXTRUDER_TEMP 160
#define USE_ADVANCE
#define ENABLE_QUADRATIC_ADVANCE
#define BAUDRATE 115200
#define ENABLE_POWER_ON_STARTUP
#define POWER_INVERTING false
#define KILL_METHOD 1
#define GCODE_BUFFER_SIZE 2
#define ACK_WITH_LINENUMBER
#define WAITING_IDENTIFIER "wait"
#define ECHO_ON_EXECUTE
#define EEPROM_MODE 0
#define FEATURE_TWO_XSTEPPER false
#define X2_STEP_PIN   E1_STEP_PIN
#define X2_DIR_PIN    E1_DIR_PIN
#define X2_ENABLE_PIN E1_ENABLE_PIN
#define FEATURE_TWO_YSTEPPER false
#define Y2_STEP_PIN   E1_STEP_PIN
#define Y2_DIR_PIN    E1_DIR_PIN
#define Y2_ENABLE_PIN E1_ENABLE_PIN
#define FEATURE_TWO_ZSTEPPER false
#define Z2_STEP_PIN   E1_STEP_PIN
#define Z2_DIR_PIN    E1_DIR_PIN
#define Z2_ENABLE_PIN E1_ENABLE_PIN
#define FEATURE_DITTO_PRINTING false
#define FEATURE_SERVO false
#define SERVO0_PIN 11
#define SERVO1_PIN 6
#define SERVO2_PIN 5
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

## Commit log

2013-12-03 added d-profile pulley
    [12toothT5_Dshaft.stl]
2013-12-05 added calibration_cube.stl
    [calibration_cube.stl]
2013-12-05 added correct calibration_cube.stl
    [calibration_cube.stl]
2013-12-05 added Repetier-Firmware for delta
    [Configuration.h]
2013-12-05 Traxxas BOM added
    [MOST Delta BOM traxxas.ods]
2014-03-25 updated SCAD, STL and BOM
    [12toothT5_Dshaft.stl, Configuration.h, MOST Delta BOM traxxas.ods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]
2014-05-18 Fixed RepetierFirmware
    [Configuration.h]
2014-05-29 Updated repetier to latest
    [Configuration.h]
2014-07-02 Updated BOM and Repetier
    [Configuration.h, MOST_Delta_BOM.ods]
2014-07-16 update for workshop
    [Configuration.h]
2014-07-28 updated stls
    [carriage.stl, effector.stl, end_idler.stl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]
2014-07-28 fixed oops
    [extruder.stl]
2014-08-26 corrected carriage stl
    [12toothT5_Dshaft.stl, carriage.stl, extdrive.stl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]
2014-11-20 corrected BOM
    [MOST_Delta_BOM.ods]
2016-07-29 Added barrel connector housing
    [barrel_connector.stl]

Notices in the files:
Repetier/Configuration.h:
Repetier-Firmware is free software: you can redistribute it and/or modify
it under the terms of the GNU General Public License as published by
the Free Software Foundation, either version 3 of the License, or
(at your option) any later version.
